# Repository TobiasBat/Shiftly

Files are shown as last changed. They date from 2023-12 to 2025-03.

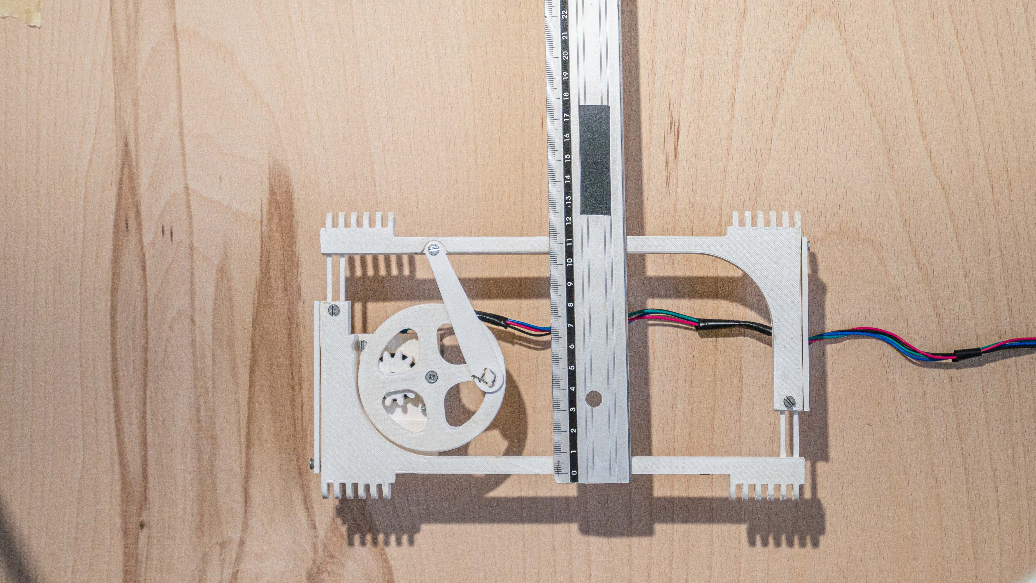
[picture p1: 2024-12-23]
Kinematic-model/evaluation/width/kin-eval-90.jpg

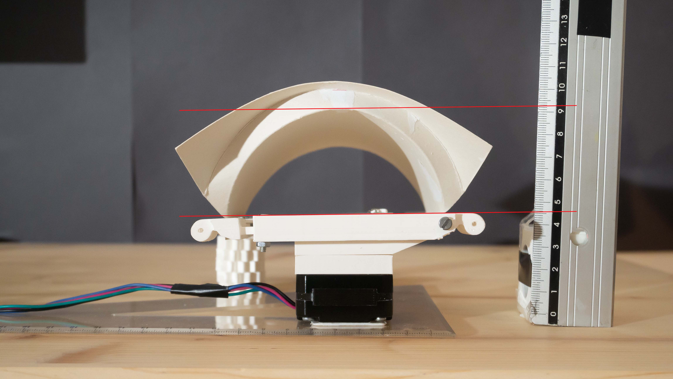
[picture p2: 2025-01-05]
Kinematic-model/evaluation/height/kin-eval-height-2.jpg

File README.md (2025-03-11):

# Shiftly

Shiftly is a novel shape-shifting haptic device that renders plausible haptic feedback when touching virtual objects in VR. By changing its shape, different geometries of virtual objects can be approximated to provide haptic feedback for the user’s hand. 

This repo contains the CAD files to print the device, the microcontroller for the device, and the VR application used to evaluate Shiftly.

If you use any information or material from this repo, please cite this publication: 

*T. Batik, H. Brument, K. Vasylevska and H. Kaufmann, "Shiftly: A Novel Origami Shape-Shifting Haptic Device for Virtual Reality," in IEEE Transactions on Visualization and Computer Graphics, doi: 10.1109/TVCG.2025.3549548.*

More detailed information about the fabrication of the prototype and the integration of the different parts can be found in my thesis: 

*Batik, T. (2023). Design and evaluation of a novel shape changing haptic device for virtual reality [Diploma Thesis, Technische Universität Wien]. reposiTUm. https://doi.org/10.34726/hss.2023.111843*

## Content

The content of this repo is aimed at making the results of *Shiftly: A Novel Origami Shape-Shifting Haptic Device for Virtual Reality* reproducible. 

* `Device` contains the stl files that are used to print Shiftly and the origami pattern. 
* `Kinematic Model` contains a sample implementation of the Kinematic model outlined in [1] and the evaluation results.
* `Microcontroller-control-program` contains the microcontroller code that runs on the device.
* `VR-Apps` The Unity source code for the VR applications to evaluate and show the capabilities of Shiftly.

#### Device

CAD and 3D printed files for Shiftly. We printed the parts in standard PLA on an FDM printer—especially the mechanical parts requiring extensive post-processing. Generally, CAD files are designed with relatively small tolerances and need, in our case, the removal of a lot of material after printing. The fusin360 files are also included; feel free to adapt the files to suit your printer. Further details about assembling are outlined in [[2]](https://doi.org/10.34726/hss.2023.111843).

#### Kinematic-model

The ` Kinematic-model/evaluation ` folder contains the images of the results of the evaluation of the kinematic model in [1]. `Kinematic-model/sample-code` contains a sample Python implementation of the kinematic model outlined in [1]. 

#### Microcontroller Control Program

This program is used on Shiftly's microcontroller to handle the communication between the VR application and the microcontroller and control the motor rotation.

The Program was tested and developed for an ESP32-DevKitC V4 board using MicroPython 1.21.0. The required hardware elements, the program's functionality, and a corresponding circuit diagram can be found in [[2]](https://doi.org/10.34726/hss.2023.111843). The communication between the microcontroller and the PC VR application is implemented via USB and Wifi — booth APIs over the same functionality.

#### VR-Apps

The VR applications that are used to test and evaluate Shiftly. Implemented in Unity 2021.3. For a HTC VIVE, Leap Motion Controller, and a VIVE tracker 2.0. More details in [[2]](https://doi.org/10.34726/hss.2023.111843).

----

[1] Shiftly: A Novel Origami Shape-Shifting Haptic Device for Virtual Reality
Tobias Batik, Hugo Brument, Khrystyna Vasylevska, Hannes Kaufmann, Currently in Review, 2025

[2] Batik, T. (2023). Design and evaluation of a novel shape changing haptic device for virtual reality [Diploma Thesis, Technische Universität Wien]. reposiTUm. https://doi.org/10.34726/hss.2023.111843

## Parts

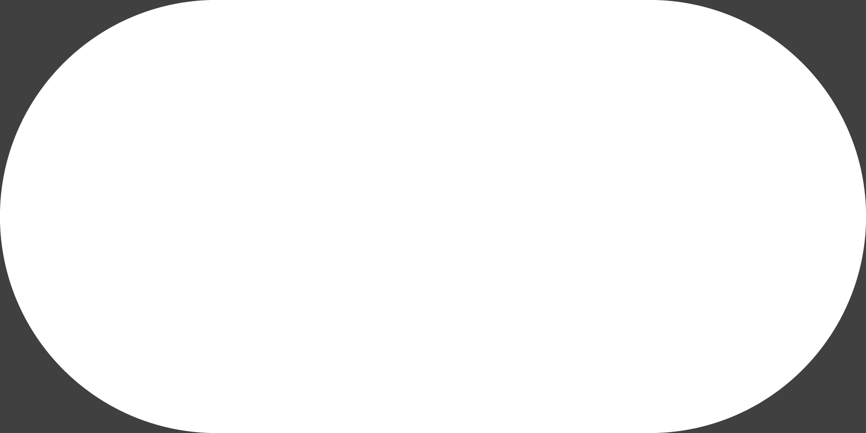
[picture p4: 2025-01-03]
VR-Apps/Assets/Materials/UI-Sprites/rounded-button-sprite-small.png

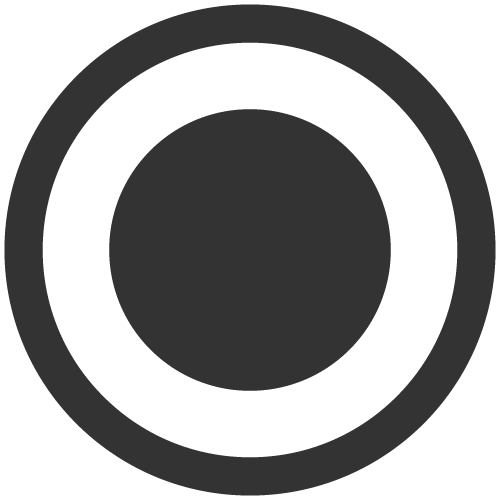
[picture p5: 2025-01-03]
VR-Apps/Assets/Materials/UI-Spreads/RadionButton-Aktive.png

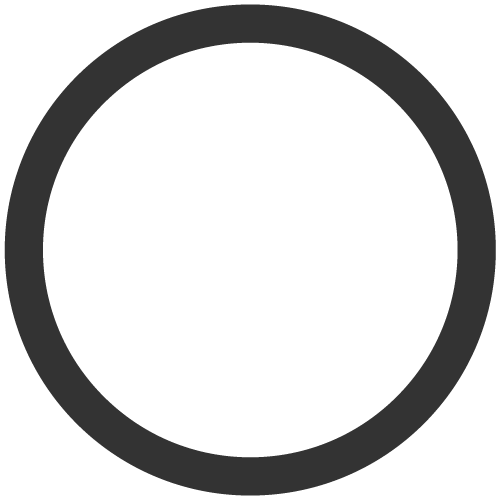
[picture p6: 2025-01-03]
VR-Apps/Assets/Materials/UI-Spreads/RadionButton-Inaktive.png

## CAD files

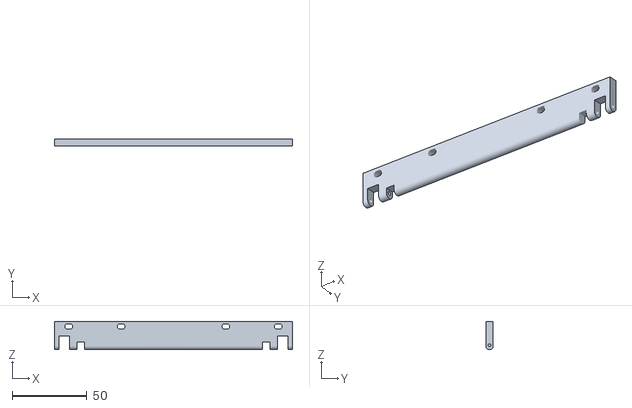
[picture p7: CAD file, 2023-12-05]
Device/stl-files/frame-attachments/Shiftly-tablestand-part-2.stl
159.0 x 5.00 x 19.0

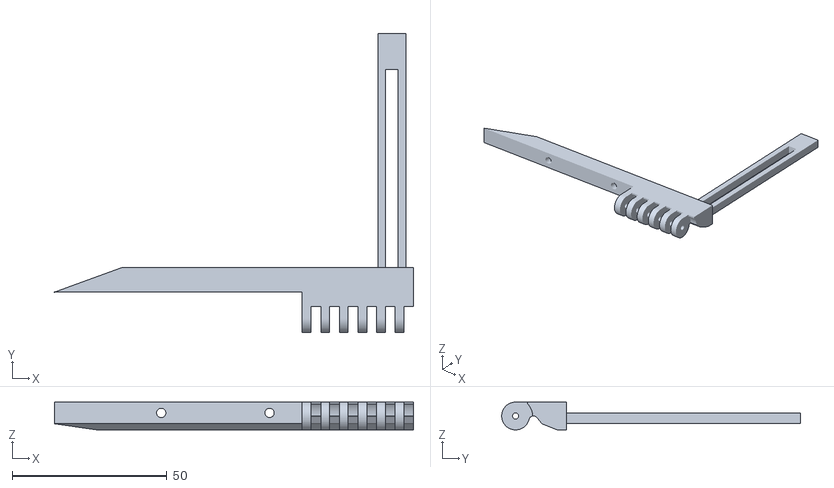
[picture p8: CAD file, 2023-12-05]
Device/stl-files/frame-motor-in-center/shiftly-frame-centermotor-otherside-male.stl
116.0 x 96.5 x 9.00

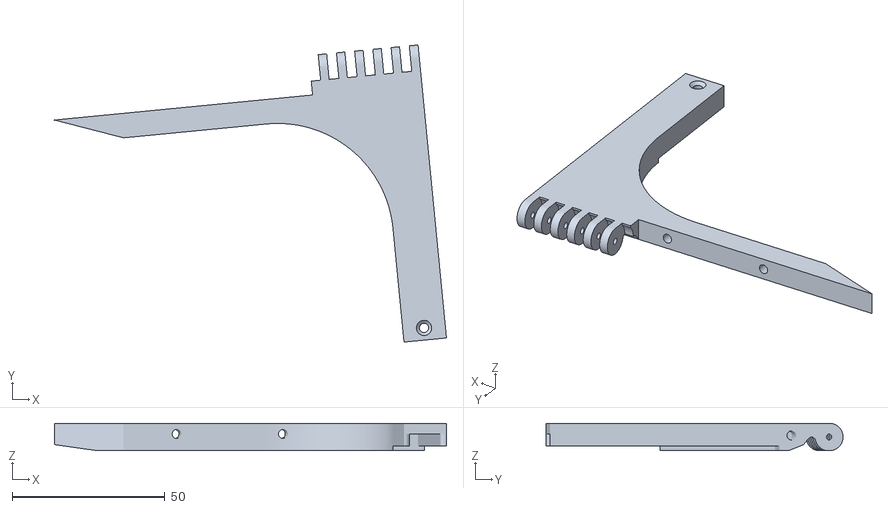
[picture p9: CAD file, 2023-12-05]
Device/stl-files/frame-motor-on-side/shiftly-frame-otherside-female.stl
128.5 x 97.4 x 9.00

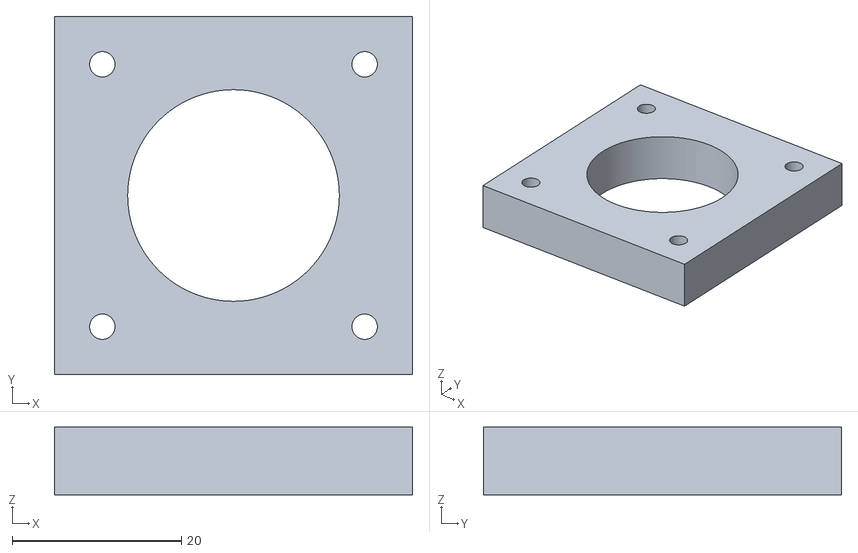
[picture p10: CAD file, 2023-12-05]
Device/stl-files/shiftly-8mm-motor-adapter.stl
42.3 x 42.3 x 8.00

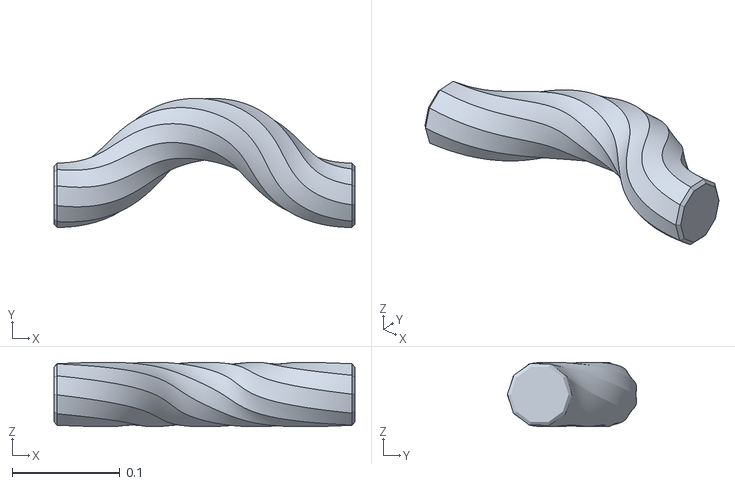
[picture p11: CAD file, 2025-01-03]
VR-Apps/Assets/Models/Object Circle/wave-10-corner-180degreetwitst.obj
0.28 x 0.12 x 0.06

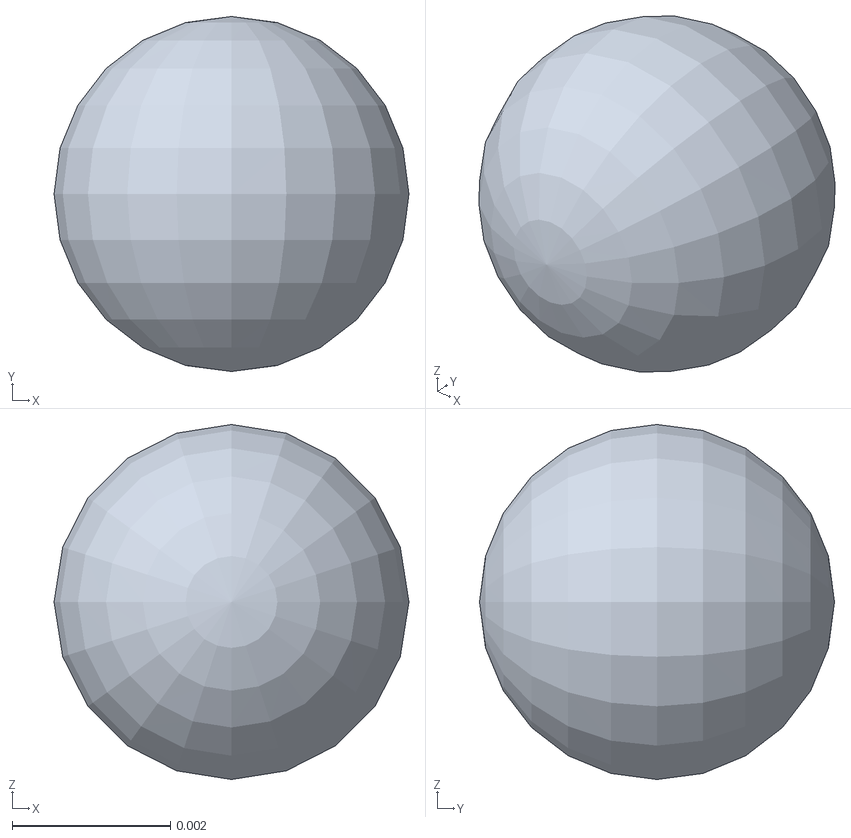
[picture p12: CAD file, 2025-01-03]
VR-Apps/Assets/Models/vr_controller_vive_1_5/trackpad_touch.obj
0.00449 x 0.00449 x 0.00449

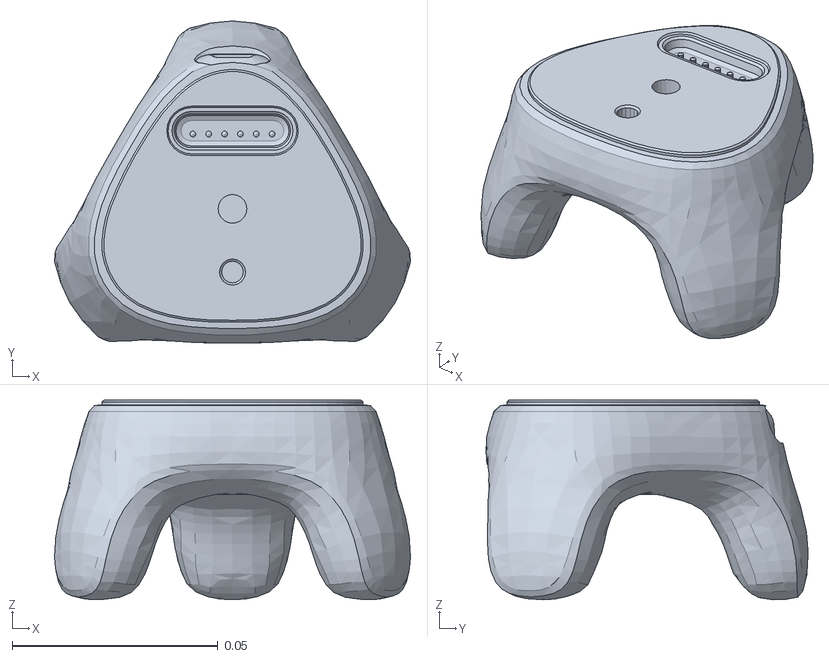
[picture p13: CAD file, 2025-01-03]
VR-Apps/Assets/Models/vr_tracker_vive_3_0.obj
0.0865 x 0.0783 x 0.0485

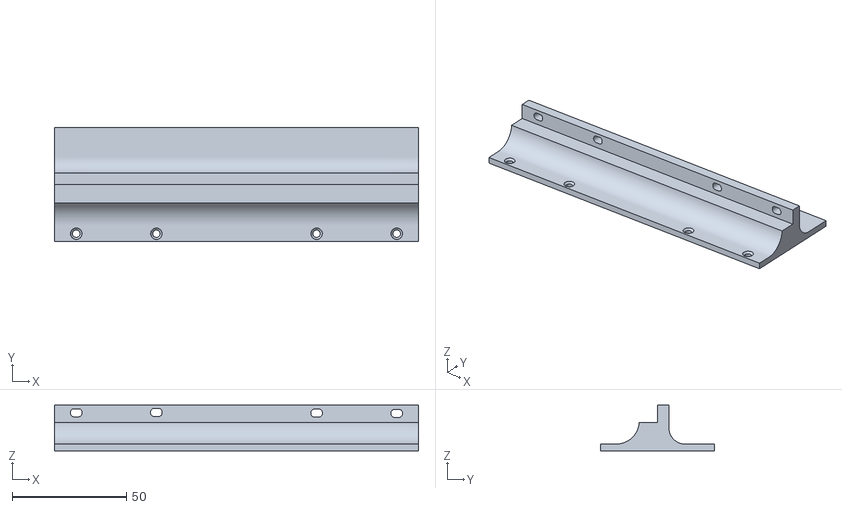
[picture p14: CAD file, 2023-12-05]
Device/stl-files/frame-attachments/Shiftly-tablestand-part-1.stl
159.0 x 50.0 x 20.0

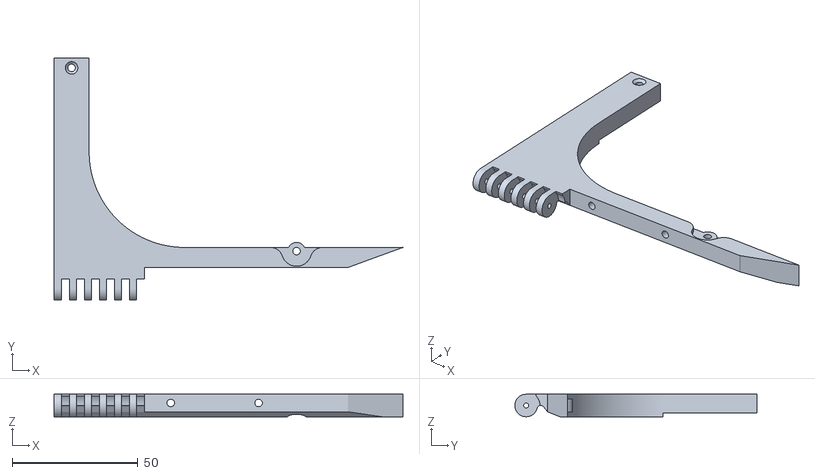
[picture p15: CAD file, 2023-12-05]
Device/stl-files/frame-motor-in-center/shiftly-frame-centermotor-otherside-female.stl
139.0 x 96.5 x 9.00

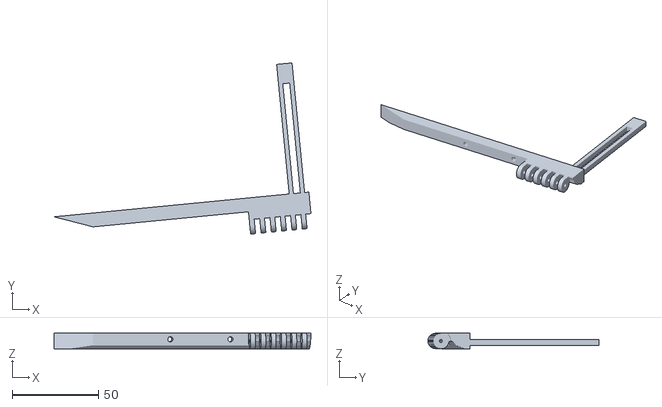
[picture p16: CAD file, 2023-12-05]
Device/stl-files/frame-motor-on-side/shiftly-frame-motorside-male.stl
149.0 x 99.3 x 9.00

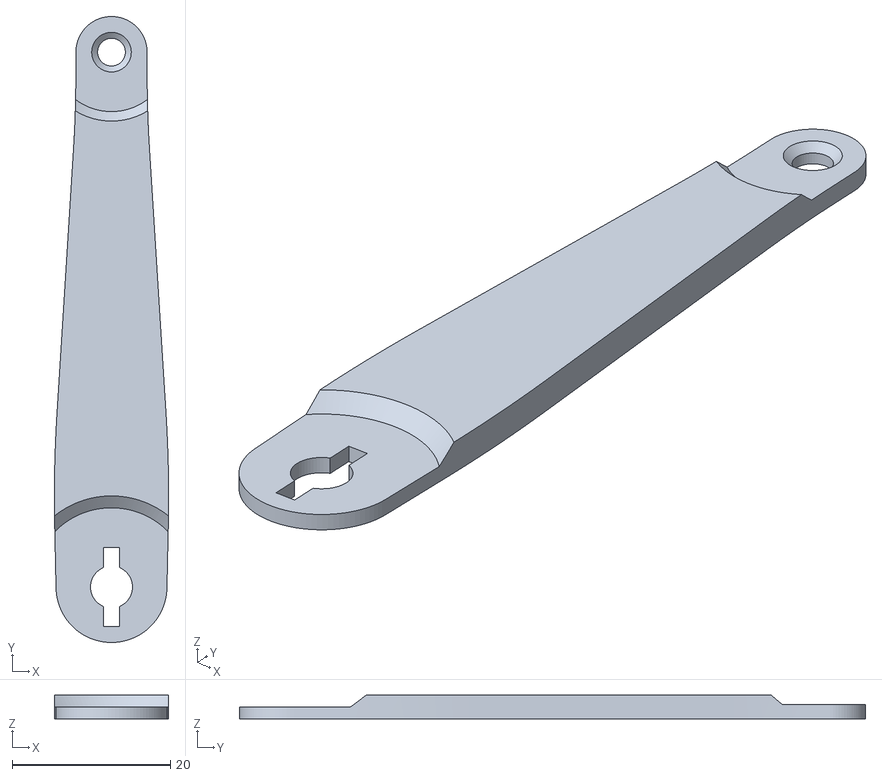
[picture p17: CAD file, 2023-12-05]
Device/stl-files/shiftly-rod.stl
14.4 x 79.0 x 3.00

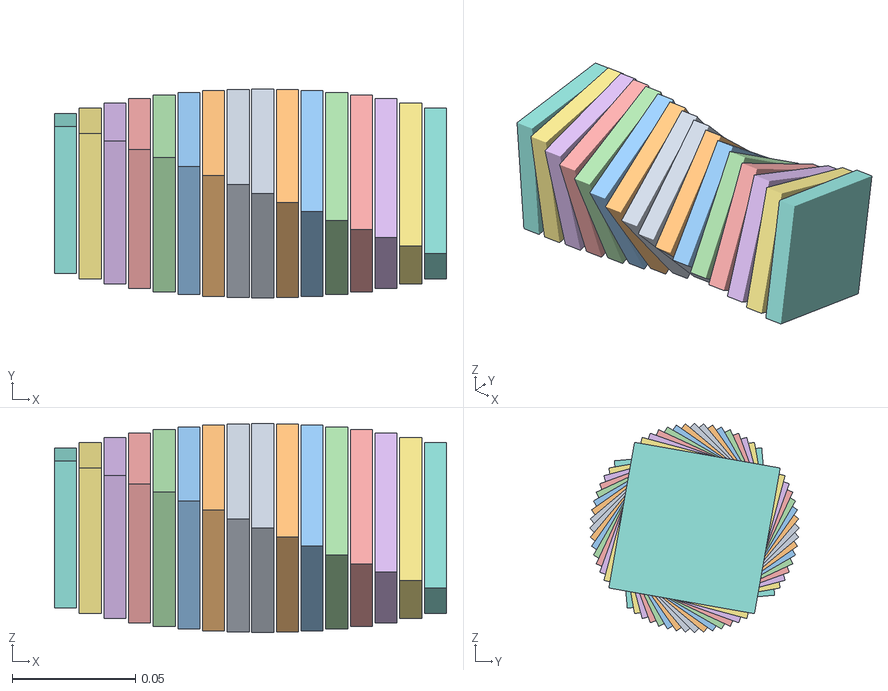
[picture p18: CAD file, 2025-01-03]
VR-Apps/Assets/Models/Object Circle/rotated-diamonds.obj
0.159 x 0.0849 x 0.0849

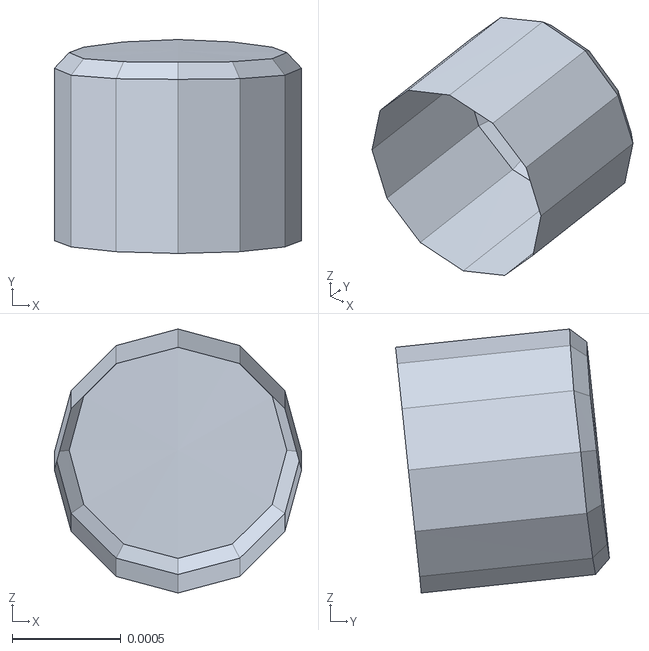
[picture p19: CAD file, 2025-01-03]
VR-Apps/Assets/Models/vr_controller_vive_1_5/led.obj
0.00114 x 0.000983 x 0.00121

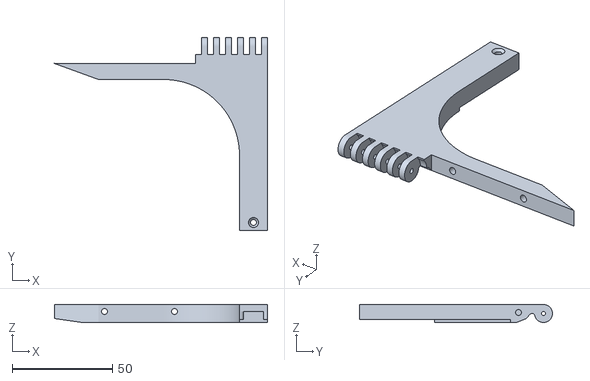
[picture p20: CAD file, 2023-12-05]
Device/stl-files/frame-motor-in-center/shiftly-frame-centermotor-motorside-male.stl
106.5 x 96.5 x 9.00

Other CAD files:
Device/stl-files/frame-motor-on-side/shiftly-frame-motoside-female.stl
VR-Apps/Assets/Models/Object Circle/shape-tester-room.obj
VR-Apps/Assets/Models/vr_controller_vive_1_5/status.obj
Device/stl-files/frame-attachments/Shiftly-tablestand-wheel.stl
Device/fusion-360/shiftly-vive-tracker-mount.f3d
Device/stl-files/frame-attachments/Shiftly-Vive-tracker-screw-on-mount.stl
Device/stl-files/frame-motor-in-center/shiftly-frame-centermotor-motorside-female.stl
Device/stl-files/frame-motor-on-side/shiftly-frame-otherside-male.stl
Device/stl-files/shiftly-motor-gear-12-long-shaft.stl
Device/stl-files/shiftly-motor-gear-12.stl
Device/stl-files/shiftly-origami-clamp.stl
Device/stl-files/shiftly-outher-gear-32-thicker-shaft.stl
Device/stl-files/shiftly-screw-cover-light.stl
VR-Apps/Assets/Models/Object Circle/Cylinder.obj
VR-Apps/Assets/Models/Object Circle/Flatt Wave.obj
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

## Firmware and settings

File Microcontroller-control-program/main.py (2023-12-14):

import time
import utime
import uasyncio
import _thread
import socket
import sys
from machine import Pin
from steppercontroller import StepperController
from esp32_utilities import ESP32Utilities


# Turns a Stepper to a certain degree
def turnStepperToDegree(stepper, degree, micro_steps,breakMilliSeconds, counting):
    while stepper.getTurning():
        print('waiting line')
        time.sleep_ms(100)
    
    stepper.turning = True
    print('Startin a new Stepper Motion', stepper.id, 'to degree', degree, ' with thread id', _thread.get_ident(), 'counting: ', counting)
    if counting: 
        stepper.turnToDegree(degree, micro_steps, breakMilliSeconds)
    else: 
        stepper.turnDegreesWithoutCounting(degree, micro_steps, breakMilliSeconds)
    stepper.turning = False
    _thread.exit()

# Serial Communication
# Gets the serial command lines 
def handleSerialCommunication():
    print('Starting to Handle Serial Communication')

    while True:
        data = sys.stdin.readline()
        parseASerialCommand(data)

# Parses the first instruction of the serial command line
def parseASerialCommand(serialLine):
    try: 
        serialLine = serialLine.strip("\n")
        arguments = serialLine.split(' ')
        firstArgument = arguments[0]
        if firstArgument == 'step':
            handleStepSerialCommand(arguments)
        elif firstArgument == 'set':
            handleSetSerialCommand(arguments)
        else: 
            handleDegreeSerialCommand(arguments)
    except:
        print('Could not parse instruction line', serialLine)

# Handles a serial command line of the form: 
#   set stepper=3 degree=0
def handleSetSerialCommand(arguments):
    try:
        stepper = ''
        degree = '' 
        for argument in arguments:
            parts = argument.split("=")
            if len(parts) > 1: 
                if parts[0] == 'stepper':
                    name = parts[1]
                    if name == '1': 
                        stepper = stepper_1
                    elif name == '2':
                        stepper = stepper_2
                    elif name == '3':
                        stepper = stepper_3
                elif parts[0] == 'degree':
                    degree = int(parts[1])
        if stepper !=  '' and degree != '':
            stepper.setDegree(degree)
        else: 
            print('stepper:', stepper, ' degree: ', degree)
    except:
        print('Could not completely execute set command')
    
# Handles a serial command line of the form:
#   step stepper=3 degree=100 microsteps=8
def handleStepSerialCommand(arguments):
    handleDegreeSerialCommand(arguments, counting = False)

# Handles a serial command of the form: 
#   stepper=3 degree=360 microsteps=8
def handleDegreeSerialCommand(arguments, counting = True):
    stepper = ''
    degree = ''
    microSteps = ''
    for argument in arguments: 
        parts = argument.split('=')
        if len(parts) > 1: 
            if parts[0] == 'stepper': 
                # Parse stepper name 
                name = parts[1]
                if name == '1': 
                    stepper = stepper_1
                elif name == '2':
                    stepper = stepper_2
                elif name == '3':
                    stepper = stepper_3
            elif parts[0] == 'degree': 
                degree = int(parts[1])
            elif parts[0] == 'microsteps':
                microSteps = int(parts[1])
    if stepper !=  '' and degree != '' and microSteps != '': 
        if counting:
            _thread.start_new_thread(turnStepperToDegree, (stepper, degree, microSteps, 1, True))
        else: 
            _thread.start_new_thread(turnStepperToDegree, (stepper, degree, microSteps, 1, False))

def parseUrlArguments(arguments): 
    a = 0
    url_parameters = arguments.split('&')
    stepper_name = ''
    stepper_degree = ''
    stepper_microsteps = ''

    for a in url_parameters:
        if 'stepper' in a:
            stepper_name = a.split('=')[1]
        elif 'degree' in a:
            stepper_degree = int(a.split('=')[1])
        elif 'microsteps' in a: 
            stepper_microsteps = int(a.split("=")[1])
    return stepper_name, stepper_degree, stepper_microsteps

def parseStepperNameToStepper(stepper_name): 
    stepper = stepper_1
    if '2' in stepper_name: 
        stepper = stepper_2
    elif '3' in stepper_name: 
        stepper = stepper_3
    return stepper
    
## Handle Server Communication
def handlingServerCommunication(): 
    print('Startin the Server\n')
    socket_ = socket.socket(socket.AF_INET, socket.SOCK_STREAM)
    socket_.bind(('', 80))
    socket_.listen(5)

    print('Server is Listening')

    while True:
        conn, addr = socket_.accept()
        try: 
            request = conn.recv(1024)
            request = request.decode().strip().split('\n', 1)
            firstLine = request[0].split(' ')
            request_type = firstLine[0]

            print(request_type, str(addr), firstLine[1])
            
            if 'PUT' in request_type:
                arguments = firstLine[1].split('?', 1)[1]
                commandPart = firstLine[1].split('?', 1)[0]
                
                command = ''
                if len(commandPart) > 1: 
                    command = commandPart.split('/', 1)[1]
                
                stepper_name, stepper_degree, stepper_microsteps = parseUrlArguments(arguments)

                # If request contains name and degree and speed
                if command == '' and stepper_name != '' and stepper_degree != '' and stepper_microsteps != '':
                    stepper = parseStepperNameToStepper(stepper_name)
                    _thread.start_new_thread(turnStepperToDegree, (stepper, stepper_degree, stepper_microsteps, 1, True))
                    conn.send('HTTP/1.1 200 OK\n')
                elif command == 'step' and stepper_name != '' and stepper_degree != '' and stepper_microsteps != '': 
                    stepper = parseStepperNameToStepper(stepper_name)
                    _thread.start_new_thread(turnStepperToDegree, (stepper, stepper_degree, stepper_microsteps, 1, False))
                    conn.send('HTTP/1.1 200 OK\n')
                elif command == 'set' and stepper_name != '' and stepper_degree != '':
                    stepper = parseStepperNameToStepper(stepper_name)
                    stepper.setDegree(stepper_degree)
                    conn.send('HTTP/1.1 200 OK\n')
                else:
                    print(' Something went wrong and argument Missing', stepper_name, stepper_degree, stepper_microsteps)
                    conn.send('HTTP/1.1 400 Bad Request\n')

            else: 
                print(' Request not supported')
                conn.send('HTTP/1.1 400 Bad Request\n')
                conn.send('Request not supported')

        except:
            print('Something went wrong with processing request')
            conn.send('HTTP/1.1 400 Bad Request\n')
        
        conn.send('Connection: close\n\n')
        print('closing connection\n')
        conn.close()



##################
#
# Main Program
#
##################

# PARAMETERS
# Stepper 1 Pin Numbers
stepper_1_directionPinNumber = 15 # on the old board is 2
stepper_1_stepPinNumber = 2 # on the old board is 15
stepper_1_ms1_pinNumber = 16
stepper_1_ms2_pinNumber = 4
stepper_1_ms3_pinNumber = 0

# Stepper 2 Pin Number
stepper_2_directionPinNumber = 17
stepper_2_stepPinNumber = 5
stepper_2_ms1_pinNumber = 21
stepper_2_ms2_pinNumber = 19
stepper_2_ms3_pinNumber = 18

# Stepper 3 Pin Number
stepper_3_directionPinNumber = 22
stepper_3_stepPinNumber = 23
stepper_3_ms1_pinNumber = 32
stepper_3_ms2_pinNumber = 33
stepper_3_ms3_pinNumber = 25

useWirelessCommunication = True
network_name =  'some network name'
network_password = 'some network password'


print('\nHello Welcome to Shiftly\n')

stepper_1 = StepperController(1, stepper_1_directionPinNumber, stepper_1_stepPinNumber, 
                                    ms1_pinNumber=stepper_1_ms1_pinNumber,
                                    ms2_pinNumber=stepper_1_ms2_pinNumber,
                                    ms3_pinNumber=stepper_1_ms3_pinNumber,
                                    micro_steps=8,
                                    ratio=(32/12)
                                    )

stepper_2 = StepperController(2, stepper_2_directionPinNumber, stepper_2_stepPinNumber,
                                    ms1_pinNumber=stepper_2_ms1_pinNumber,
                                    ms2_pinNumber=stepper_2_ms2_pinNumber,
                                    ms3_pinNumber=stepper_2_ms3_pinNumber,
                                    micro_steps=8,
                                    ratio=(32/12)
                                    )
stepper_3 = StepperController(3, stepper_3_directionPinNumber, stepper_3_stepPinNumber,
                                    ms1_pinNumber=stepper_3_ms1_pinNumber,
                                    ms2_pinNumber=stepper_3_ms2_pinNumber,
                                    ms3_pinNumber=stepper_3_ms3_pinNumber,
                                    micro_steps=8,
                                    ratio=(32/12)
                            )


if useWirelessCommunication: 
    connectedToNetwork = ESP32Utilities().connectToNetwork(network_name, network_password)

    time.sleep(1)

    if not connectedToNetwork:
        print('Not connected to Wifi')
        handleSerialCommunication()
    else:
        handlingServerCommunication()
else: 
    handleSerialCommunication()

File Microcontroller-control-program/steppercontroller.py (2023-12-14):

import time
import math
from machine import Pin

class StepperController: 
    # PINS
    STEP_PIN = Pin(16, Pin.OUT)
    DIR_PIN = Pin(17, Pin.OUT)
    MS3_PIN = Pin(0, Pin.OUT)
    MS2_PIN = Pin(4, Pin.OUT)
    MS1_PIN = Pin(16, Pin.OUT)

    numberOfStepsPerRevolution = 200 * 16 
    micro_steps = 16
    ratio = 1
    id = 0
    currentStep = 0
    turning = False
    direction = True # True if clockwise
    

    def __init__(self, id ,directionPinNumber, stepPinNumber, ms1_pinNumber = 16, ms2_pinNumber = 4, ms3_pinNumber = 0, micro_steps = 16, ratio = 1):
        print('Initiating new Stepper', id, directionPinNumber, stepPinNumber)
        print('MS PIN NUMBERS: ', ms1_pinNumber, ms2_pinNumber, ms3_pinNumber, micro_steps, ratio)

        self.id = id
        #Init STEP and DIR pin
        self.STEP_PIN = Pin(stepPinNumber, Pin.OUT)
        self.STEP_PIN.off()
        self.DIR_PIN = Pin(directionPinNumber, Pin.OUT)
        self.setDirectionClockwise()

        # Set Speed Control Pins
        self.MS1_PIN = Pin(ms1_pinNumber, Pin.OUT)
        self.MS2_PIN = Pin(ms2_pinNumber, Pin.OUT)
        self.MS3_PIN = Pin(ms3_pinNumber, Pin.OUT)

        self.ratio = ratio
        self.micro_steps = micro_steps
        self.updateSpeed()


    def updateSpeed(self): 
        self.numberOfStepsPerRevolution = 200 * self.micro_steps * self.ratio

        if self.micro_steps == 16:
            self.MS1_PIN.on()
            self.MS2_PIN.on()
            self.MS3_PIN.on()
            
        elif self.micro_steps == 8: 
            self.MS1_PIN.on()
            self.MS2_PIN.on()
            self.MS3_PIN.off()

        elif self.micro_steps == 4: 
            self.MS1_PIN.off()
            self.MS2_PIN.on()
            self.MS3_PIN.off()
        
        elif self.micro_steps == 2: 
            self.MS1_PIN.on()
            self.MS2_PIN.off()
            self.MS3_PIN.off()
        
        elif self.micro_steps == 1: 
            self.MS1_PIN.off()
            self.MS2_PIN.off()
            self.MS3_PIN.off()

        else: 
            self.MS1_PIN.on()
            self.MS2_PIN.on()
            self.MS3_PIN.on()


    def setDegree(self, degree):
        self.currentStep = self.numberOfStepsPerRevolution / 360.0 * degree
        print('set stepper to ', self.currentStep, ' or ', degree , ' degree.')
        self.printStateOfStepper()

    def setDirectionClockwise(self): 
        self.DIR_PIN.on()
        self.direction = True

    def setDirectionCounterClockWise(self): 
        self.DIR_PIN.off()
        self.direction = False

    def turn360degree(self, breakMilliSeconds): 
        print('Turning ', self.id)
        
        update = 1
        if not self.direction:
            update = -1
        
        for i in range(0, self.numberOfStepsPerRevolution):
            self.STEP_PIN.on()
            time.sleep_ms(breakMilliSeconds)
            self.STEP_PIN.off()
            self.currentStep = (self.currentStep + update) % self.numberOfStepsPerRevolution
            time.sleep_ms(breakMilliSeconds)
        
        print('Motor', self.id, ':', self.currentStep )
    
    def turnDegree(self, degree, breakMilliSeconds): 
        numberOfSteps = (degree / 360.0) * self.numberOfStepsPerRevolution
        self.turnSteeps(numberOfSteps, breakMilliSeconds)

    def turnDegreesWithoutCounting(self, degree, micro_steps, breakMilliSeconds): 
        if self.micro_steps != micro_steps: 
            self.updateMicroSteps(micro_steps)
        numberOfSteps = (degree / 360.0) * self.numberOfStepsPerRevolution
        self.turnStepsWithoutCounting(numberOfSteps, breakMilliSeconds)

    def turnSteeps(self, steps, breakMilliSeconds):
        update = 1
        if (steps < 0):
            self.setDirectionCounterClockWise()
            update = -1
        else: 
            self.setDirectionClockwise()
        
        for i in range(0, math.fabs(steps)):
            self.STEP_PIN.on()
            time.sleep_ms(breakMilliSeconds)
            self.STEP_PIN.off()
            self.currentStep = (self.currentStep + update) % self.numberOfStepsPerRevolution
            time.sleep_ms(breakMilliSeconds)
        self.printStateOfStepper()

    def turnStepsWithoutCounting(self, steps, breakMilliSeconds):
        update = 1
        if (steps < 0):
            self.setDirectionCounterClockWise()
            update = -1
        else: 
            self.setDirectionClockwise()
        
        for i in range(0, math.fabs(steps)):
            self.STEP_PIN.on()
            time.sleep_ms(breakMilliSeconds)
            self.STEP_PIN.off()
            # self.currentStep = (self.currentStep + update) % self.numberOfStepsPerRevolution
            time.sleep_ms(breakMilliSeconds)
        self.printStateOfStepper()

    def turnToDegree(self, degree, micro_steps, breakMilliSeconds): 
        if self.micro_steps != micro_steps: 
            self.updateMicroSteps(micro_steps)
        
        directionStep = degree / 360 * self.numberOfStepsPerRevolution
        deltaSteps = 0
        if (self.currentStep == directionStep): 
            print('Stepper', self.id, 'No motion required')
            return
        if (self.currentStep > directionStep): 
            # means negativ change 
            deltaSteps = (self.currentStep - directionStep) * (-1.0)
        else: 
            deltaSteps = (directionStep - self.currentStep)

        print('Delta Steps', deltaSteps)
        self.turnSteeps(deltaSteps, breakMilliSeconds)

    def updateMicroSteps(self, micro_steps): 
        if micro_steps == 16 or micro_steps == 8 or micro_steps == 4 or micro_steps == 2 or micro_steps == 1: 
            self.micro_steps = micro_steps
            self.updateSpeed()
        else: 
            print('No valid Speed', micro_steps)

    def getTurning(self):
        return self.turning
    
    def printStateOfStepper(self):
        print('Motor', 
            self.id, '-', 
            'steps: ', self.currentStep, 
            ', norm: ' , self.currentStep / self.numberOfStepsPerRevolution, 
            ', degree:',  self.currentStep / self.numberOfStepsPerRevolution * 360.0, '\n')

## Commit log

2023-12-05 Device stl files
    [Shiftly-Vive-tracker-screw-on-mount.stl, Shiftly-tablestand-part-1.stl, Shiftly-tablestand-part-2.stl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]
2023-12-14 Adding ESP32 code
2025-01-03 ADDs source and CAD files for shiftly prototype
    [shiftly-vive-tracker-mount.f3d]
2025-01-03 ADDs VR Apps
    [Cylinder.obj, Flatt Wave.obj, body.obj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]
